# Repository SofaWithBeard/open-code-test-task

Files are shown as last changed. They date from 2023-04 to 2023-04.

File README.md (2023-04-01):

# Драйвер бесколлекторного мотора с гальванической развязкой
## Входные данные для проектирования
Необходимо разработать схему для уравления мотором по следующим тербования:
* мотор - T-MOTOR MT 3515-15 400KV 
* управляющий контроллер - STM32F405RGT6
* управление должно осуществляться при помощи интерфейса USB или с помощью ШИМ.

Из [технических характеристик](http://www.himodel.com/m/electric/T-Motor_MT3515_400KV_Outrunner_Brushless_Motor_for_Multi-copter_3-8S.html) определяем, что:
* максимальный ток составляет 30 А
* напряжение питания выбираем равным 18,5 В, что соответствует 5ти ячейкам литиевых батарей с номинальным напряжением 3,7 В

## Выбор основной элементной базы и структуры устройства
При выборе элементной базы и определении структуры устройства будем исходить из того, что данный модуль при выходе из строя ремонту подлежать не будет, а производится полная его замена.
Таким образом гальваническая развязка будет осуществляться между внешними интерфейсами управления и контроллером в устройстве.

В качестве устройств для гальванической развязки выберем [ADuM3160](https://static.chipdip.ru/lib/009/DOC004009573.pdf) для интерфейса USB и [ADUM1400](https://static.chipdip.ru/lib/011/DOC004011682.pdf) для управления с помощью ШИМ сигнала. В слечае, когда подключены оба интерфейса, чтобы мажоритировать источник управления, на разъём ШИМ управления выведен дополнительный сигнал - в высоком его состоянии управление происходит посредством ШИМ, в низком - USB. По умолчанию со стороны драйвера этот сигнал имеет низкий уровень посредством подтяжки внутри микроконтроллера.

Для реализации мостовой схемы выберем транзистор [P0603BD](https://datasheetspdf.com/pdf-file/1094331/UNIKC/P0603BD/1) в следствии его большой нагрузочной способности и малого сопротивления открытого канала.

## Управление бесколлекторным двигателем
Управление осуществляется при помощи поочерёдного переключения обмоток ротора посредством полного моста на транзисторах.

Для эффективного управление трехфазным бесколлекторным двигателем необходима синхронизация управляющих воздействий и положения ротора. Для реализации используется эффект Back-EMF (за основу взят материал [отсюда](https://www.nxp.com/docs/en/application-note/AN1914.pdf)). Метод заключается в том, чтобы использовать незадействованную обмотру как индуктивный датчик. При переходе взаимного расположения статора и ротора через точку нуля, в которой напряжение, снимаемое с обмотки, будет равно половине питающего напряжения, происходит переключение моста. Это происходит до тех пор, пока не будет установлено целевое значение частоты вращения двигателя.

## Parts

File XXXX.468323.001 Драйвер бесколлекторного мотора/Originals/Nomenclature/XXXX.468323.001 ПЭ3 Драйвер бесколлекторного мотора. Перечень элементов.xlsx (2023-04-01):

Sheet: 1
Перв. примен. | Поз. обозначе- ние |  |  | Наименование |  |  |  | Кол. | Примечание
 |  |  |  | Конденсаторы
 | C1-C8 |  |  | SMD0603 X7R 50 В, 0,1мкФ±10% |  |  |  | 8
 |  |  |  | CC0603KRX7R9BB104
 | C9,C10 |  |  | SMD0603 NPO 50 В, 10пФ±5% |  |  |  | 2
 |  |  |  | CC0603JRNPO9BN100
Справ. №
 | C11 |  |  | SMD0603 X7R 50 В, 0,1мкФ±10% |  |  |  | 1
 |  |  |  | CC0603KRX7R9BB104
 | C12 |  |  | SMD0603 X5R 6,3 В, 4,7мкФ±10% |  |  |  | 1
 |  |  |  | CC0603KRX5R5BB475
 | C13 |  |  | SMD1210 Y5R 50 В, 10мкФ±-20/+80% |  |  |  | 1
 |  |  |  | CC1210ZKY5V9BB106
 | C14-C17 |  |  | SMD0603 X7R 50 В, 0,1мкФ±10% |  |  |  | 4
 |  |  |  | CC0603KRX7R9BB104
 | C18 |  |  | SMD0603 X5R 10 В, 10мкФ±10% |  |  |  | 1
 |  |  |  | CC0603KRX5R6BB106
 | C19 |  |  | SMD0603 X7R 50 В, 0,1мкФ±10% |  |  |  | 1
Подп. И дата
 |  |  |  | CC0603KRX7R9BB104
 |  |  |  | Микросхемы
 | DA1 |  |  | Линейный стабилизатор с малым падением |  |  |  | 1
 |  |  |  | напряжения 3,3В, 1А LM1117GS-3.3
Инв.№ дубл.
 | DD1 |  |  | Микросхема гальванической развязки |  |  |  | 1
 |  |  |  | ADUM1400ARWZ
 | DD2 |  |  | Микросхема гальванической развязки |  |  |  | 1
Взам. инв.№
 |  |  |  | интерфеса USB High/Low Speed ADuM3160BRWZ
 | DD3 |  |  | Микроконтроллер STM32F405RGT6 |  |  |  | 1
Подп. и дата
 |  |  |  | Резисторы
 | R1,R2 |  |  | SMD0603 0,1 Вт, 5,1 кОм±1% RC0603FR-075K1L |  |  |  | 2
 |  |  |  |  |  |  | XXXX.468323.001 ПЭ3
 | Изм. | Лист | № докум. |  | Подп. | Дата
Инв.№ подл. | Разраб. |  | Воробьев |  |  |  | Драйвер бесколлекторно двигателя | Лит. |  | Лист | Листов
 | Пров. |  |  |  |  |  |  |  |  | 1 | 2
 | Н. контр. |  |  |  |  |  | Перечень элементов
 | Утв.
 |  |  |  |  |  |  | Копировал | Формат А4

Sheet: 2
 | Поз. обозначе- ние |  |  | Наименование |  |  |  | Кол. | Примечание
 | R3 |  |  | SMD0603 0,1 Вт, 910 кОм±1% RC0603FR-07910KL |  |  |  | 1
 | R4,R5 |  |  | SMD0603 0,1 Вт, 24 Ом±1% RC0603FR-0724RL |  |  |  | 2
 | R6 |  |  | SMD0603 0,1 Вт, 30 кОм±1% RC0603FR-0730KL |  |  |  | 1
 | R7 |  |  | SMD0603 0,1 Вт, 5,6 кОм±1% RC0603FR-075K6L |  |  |  | 1
 | R8 |  |  | SMD0603 0,1 Вт, 100 кОм±1% RC0603FR-07100KL |  |  |  | 1
 | R9,R10 |  |  | SMD0603 0,1 Вт, 24 Ом±1% RC0603FR-0724RL |  |  |  | 2
 | R11,R12 |  |  | SMD0603 0,1 Вт, 10 кОм±1% RC0603FR-0710KL |  |  |  | 2
 | R13-R15 |  |  | SMD0603 0,5 Вт, 1,5 кОм±1% RC1210FR-071K5L |  |  |  | 3
 | R18 |  |  | SMD0603 0,1 Вт, 30 кОм±1% RC0603FR-0730KL |  |  |  | 1
 | R19 |  |  | SMD0603 0,1 Вт, 3,3 кОм±1% RC0603FR-073K3L |  |  |  | 1
 | R20 |  |  | SMD0603 0,1 Вт, 30 кОм±1% RC0603FR-0730KL |  |  |  | 1
 | R21 |  |  | SMD0603 0,1 Вт, 3,3 кОм±1% RC0603FR-073K3L |  |  |  | 1
 | R22-R24 |  |  | SMD0603 0,1 Вт, 5,6 кОм±1% RC0603FR-075K6L |  |  |  | 3
 |  |  |  | Транзисторы
 | VT1 |  |  | С индуцированным P-каналом -30 В, -4,0 А |  |  |  | 1
 |  |  |  | AO3401A
Подп. И дата
 | VT2-VT5 |  |  | С индуцированным N-каналом 40 В, 3,6 А |  |  |  | 4
 |  |  |  | IRLML0040TRPBF
 | VT6-VT11 |  |  | С индуцированным N-каналом 30 В, 70 А |  |  |  | 6
 |  |  |  | P0603BD
Инв.№ дубл.
 |  |  |  | Соединители
 | X1 |  |  | Разъём USB Type C USB3.1 TYPE-C 16PF-015 |  |  |  | 1
 | X2-X5 |  |  | Контактные площадки на печатной плате
Взам. инв.№
 |  |  |  | Кварцевые резонаторы
 | ZQ1 |  |  | 8МГц L-KLS14-HC-49S-8.000-16-30-C |  |  |  | 1
Подп. и дата
Инв.№ подл.
 |  |  |  |  |  |  | XXXX.468323.001 ПЭ3 |  |  | Лист
 |  |  |  |  |  |  |  |  |  | 2
 | Изм. | Лист | № докум. |  | Подп. | Дата
 |  |  |  |  |  |  | Копировал | Формат А4

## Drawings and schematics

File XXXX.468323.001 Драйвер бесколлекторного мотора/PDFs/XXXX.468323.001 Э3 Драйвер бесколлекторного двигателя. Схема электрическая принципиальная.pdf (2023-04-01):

# 16 DD2ADuM³¹⁶⁰BRWZ

Цепь Конт.

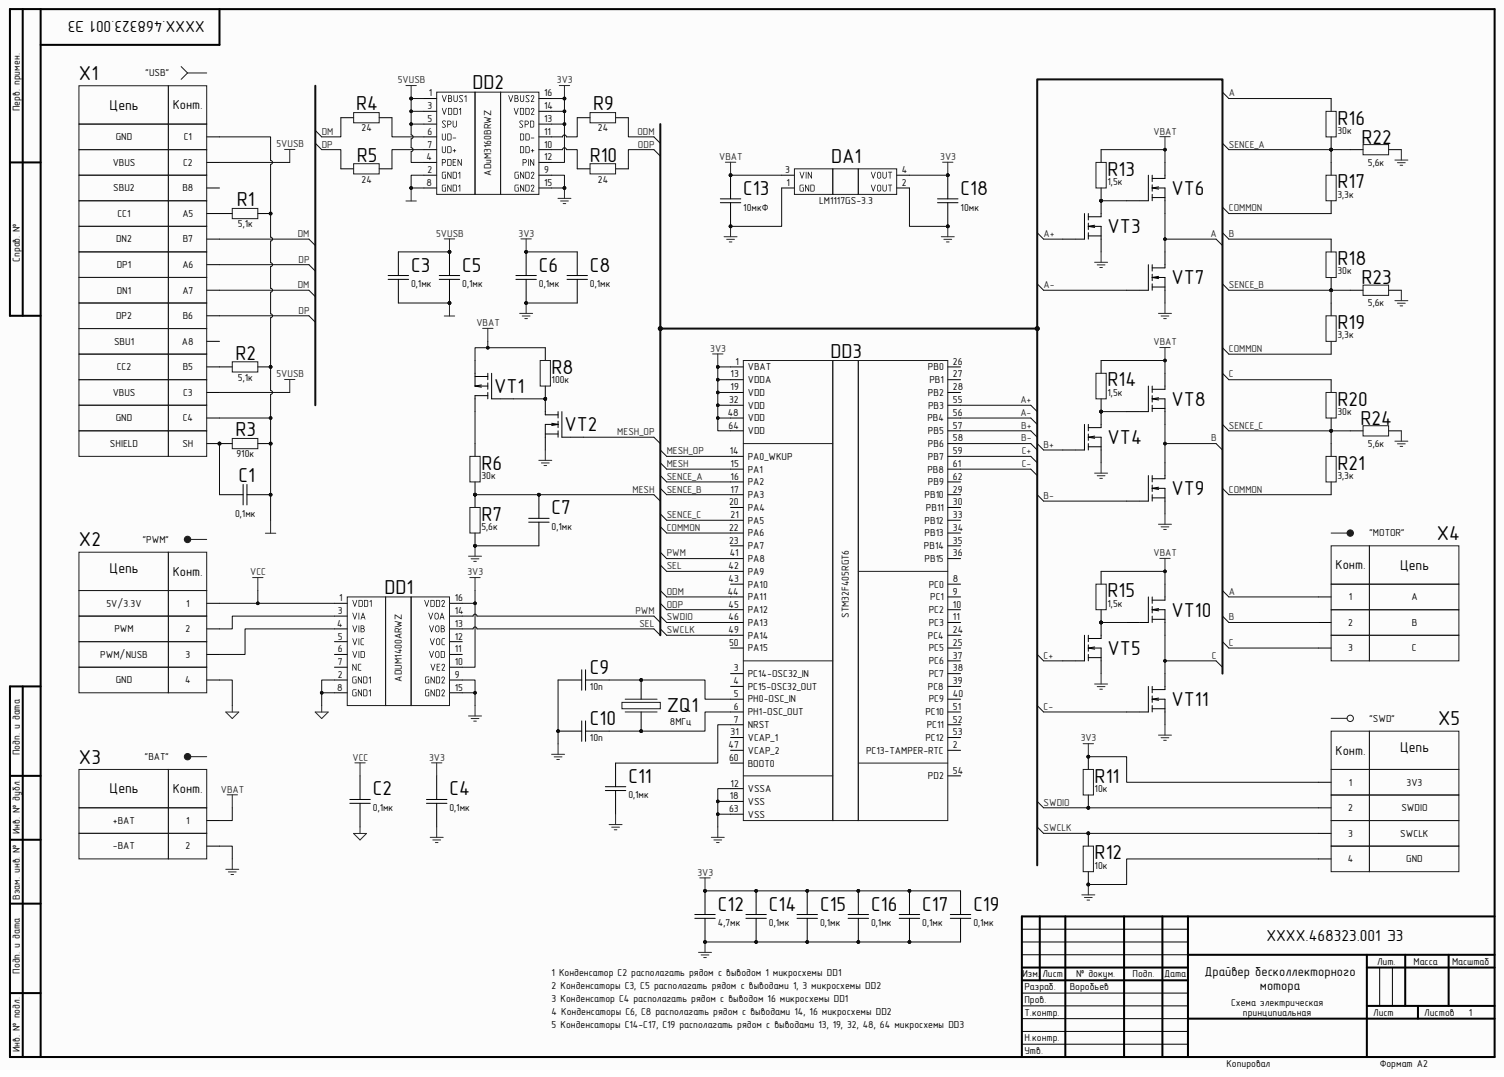
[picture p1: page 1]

Инв. № подл. Инв. № дубл. Подп. и дата Взам. инв. № Подп. и дата Перв. примен. Справ. №

XXXX.468323.001 Э3

Драйвер бесколлекторного мотора Схема электрическая принципиальная | Лит. | Масса | Масштаб

1 Конденcатор C2 располагать рядом с выводом 1 микросхемы DD1
2 Конденcаторы C3, C5 располагать рядом с выводами 1, 3 микросхемы DD2
3 Конденcатор C4 располагать рядом с выводом 16 микросхемы DD1
4 Конденcаторы C6, C8 располагать рядом с выводами 14, 16 микросхемы DD2
5 Конденcаторы С14-С17, С19 располагать рядом с выводами 13, 19, 32, 48, 64 микросхемы DD3

Изм. | Лист | № докум. | Подп. | Дата
Разраб. | | Воробьев
Пров.
Т.контр. | | | | | Лист | Листов 1

Н.контр.
Утв.

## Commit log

2023-04-01 Инициализация проекта
    [XXXX.468323.001 Драйвер бесколлекторного мотора. Схема электрическая принципиальная.SchDoc, XXXX.468323.001 Драйвер бесколлекторного мотора.PrjPcb]
2023-04-01 Изменение .ignore
2023-04-01 Удаление /History
2023-04-01 -Разработана схема электрическа принципиальная -Оформлен перечень элементов
    [XXXX.468323.001 Э3 Драйвер бесколлекторного мотора. Схема электрическая принципиальная.SchDoc]
2023-04-01 -Разработана схема электрическая принципиальная -Оформлен перечень элементов
    [XXXX.468323.001 Драйвер бесколлекторного мотора.PrjPcb, XXXX.468323.001 ПЭ3 Драйвер бесколлекторного мотора. Перечень элементов.xlsx, XXXX.468323.001 Э3 Драйве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]
2023-04-01 Проверка отображения Readme файла
2023-04-01 Пробный просмотр
2023-04-01 Оформление README файла
    [XXXX.468323.001 Э3 Драйвер бесколлекторного мотора. Схема электрическая принципиальная.SchDoc]
